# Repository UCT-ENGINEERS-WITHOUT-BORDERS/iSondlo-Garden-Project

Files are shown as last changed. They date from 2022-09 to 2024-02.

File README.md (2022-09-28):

# iSondlo-Garden-Project
For the management of work related to the Arduino-based electronic garden equipped with solar pv modules to generate power and sensors and internet connection capabilities to enable IoT features. Arduino-based embedded system includes temperature, humidity, and capacitive moisture sensors.

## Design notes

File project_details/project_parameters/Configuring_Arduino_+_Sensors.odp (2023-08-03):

## EWB iSondlo Project Configuring the Arduino & Sensors

20 October 2022

Electronics Team

## Scenario

- Garden in a 132cm x 379cm corrugated iron container
- Requires control and monitoring system to ensure that the environment yields high quality vegetables

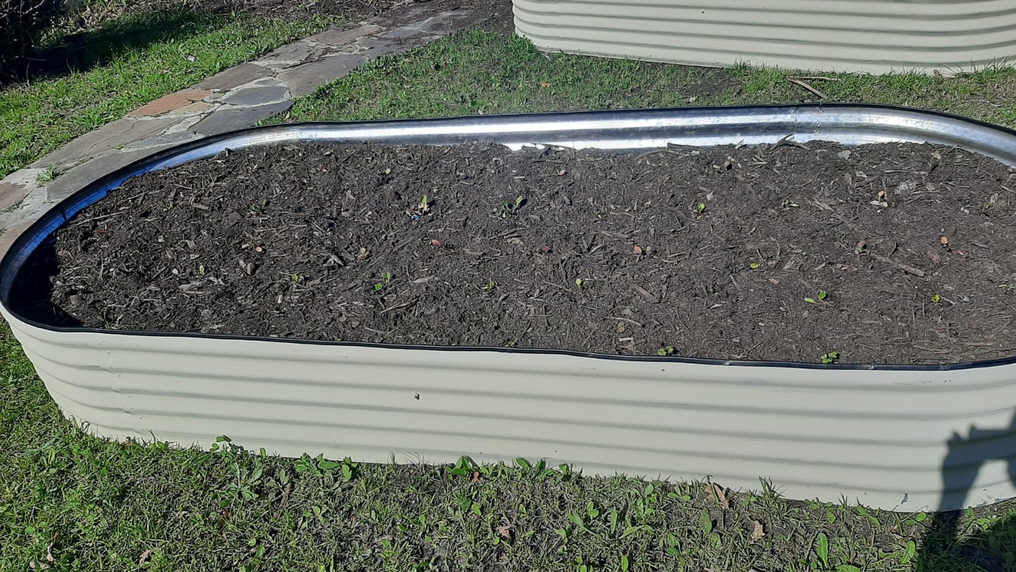
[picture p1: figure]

## Control and Monitoring System

- Garden is monitored using 4 sensors:
      - Temperature sensor:
          Maxim DS18B20 by Dallas Semiconductors
      - Soil moisture sensors:
          KE2023 Keyes moisture sensor module
      - Humidity sensor
          Ghitron HMZ-333A1
      - Light sensor
          LDR

## Control and Monitoring System

- Controls flow of water to plants using:
      - Relay switch
          KY0019 Keyestudio 5V Relay Module
      - Solenoid valve

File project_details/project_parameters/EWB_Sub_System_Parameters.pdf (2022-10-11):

Engineers Without Borders

Electronics Team:
iSondlo Garden Sub-System External Parameters and Constraints

Name: Bonga Njamela

### 10 October 2022

This aims to document the external parameters and constraints affecting the growth of plants in the iSondlo Garden. The main vegetable in the garden spinach (Spinacia oleracea).

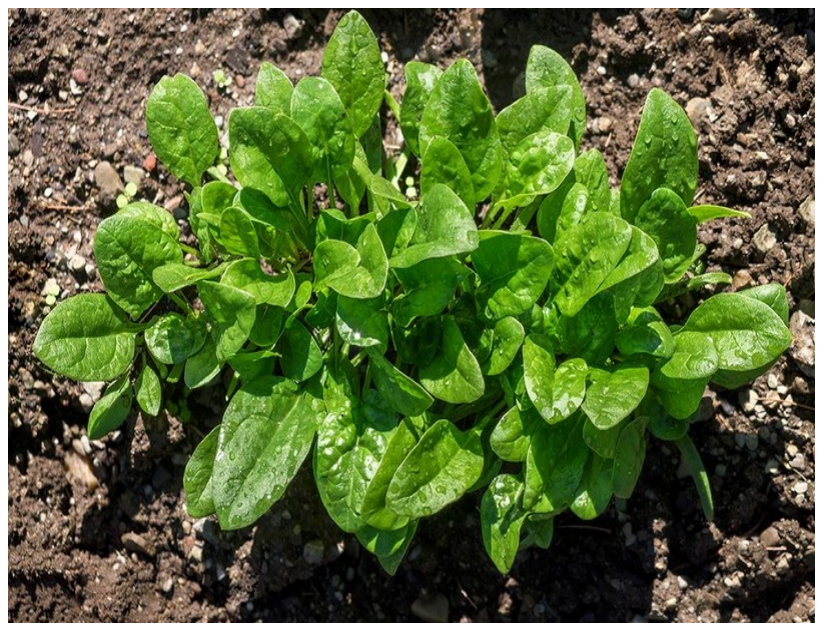
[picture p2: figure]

Some healthy looking spinach[1] (https://hips.hearstapps.com/hmg-prod/images/981/articles/2018/02/growingspinach-1000-0-1519138802.jpg)

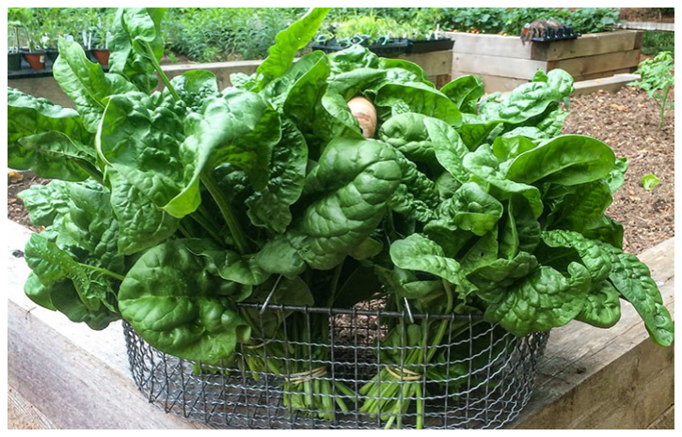
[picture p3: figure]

Ready to eat full grown spinach[2] (https://joegardener.com/wp-content/uploads/2021/04/IMG_1931-adj-708X466.jpg)

The state of the environment that the spinach grows in must be controlled to produce the best possible quality vegetable. The electronics team aims to maintain the optimum conditions for growth using an Arduino-based system. The system uses four sensors to monitor the state of the environment, namely, temperature; humidity; soil moisture; and light sensors. To maintain suitable conditions, the system controls the flow and distribution of water to the plants. We also aim to monitor and control the environment such that water is consumed in a sustainable manner.

This paper does not include the variables associated with the operation of the network connection module, and the storage and manipulation of data in the SD card module. Plant description

Spinach is a leafy vegetable which grows well in cool weather and in full sun to light shade. There are different types of spinach but each typically has smooth green leaves on a stem that grows vertically up from the soil. Spinach produces yellowish green flowers before seeding. It grows to maturity in six to eight weeks with leaves reaching 10 cm to

17 cm at maturity. It is recommended to plant spinach seeds in cool soil temperatures between 7℃ to 15℃ and to maintain the soil temperature between 16℃ and 24℃ after germination. Temperatures above the recommended range affect the taste of the spinach, making it taste more bitter. The soil moisture can be maintained and the temperature kept cool by adding mulch to the soil. The highest recorded temperature in Cape Town, in 2022, was recorded in February at 32.28℃ and the lowest recorded temperature was 8.33℃ in June[3] (https://www.ncei.noaa.gov/access/past-weather/cape%20town)

. The average temperature in between October 2021 and October 2022 was 16.11℃.

Graph showing maximum temperature trends around Cape Town International Airport[4] (https://www.ncei.noaa.gov/access/past-weather/cape%20town)

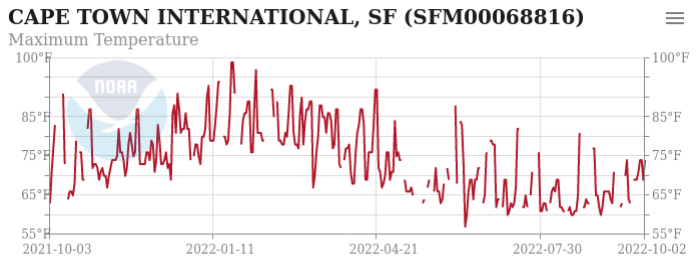
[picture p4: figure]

Spinach grows taller for days longer than 14 hours but if incident light is too bright and the temperature is too high, the plant will grow its floral stem prematurely. It requires constant soil moisture and humidity. The recommended humidity for the plants should be in the range of 90%-95%. In Cape Town, the relative humidity of the air ranges between 70% in November to 85%. Howevev, if the soil moisture and temperature needs are met, then humidity is typically not an issue.

Spinach requires to be watered frequently but without making the soil to soggy as the it will struggle to grow. Watering frequently becomes very important on days with high temperature to prohibit premature flowering. It is recommend to give spinach 2.54 cm to 3.81 cm of water per week[5]. (https://www.thespruce.com/growing-spinach-1403448) Values in this range should be achieved as an average of watering periodically rather than deeply to avoid making the soil soggy.

Each sensor has an associated variable to monitor and the Arduino is given low-value triggers, high-triggers and baselines corresponding to the recommended threshold values for each variable. To obtain suitable measurements of soil moisture, the soil moisture sensor should be calibrated to give values between 300 and 700 for 2.54 cm to 3.81 cm of water. The automated irrigation system should be calibrated to dispense the correct amount of water each time by measure the amount of time that the solenoid valve should be open.

Constant Variables and Monitored Variables

Table 1 on summarises the variables that are going to be monitored and the low-value triggers and high-value triggers associated with the minimum and maximum values for growing good quality spinach.

Table 1: Showing the variables that will be programmed in the Arduino to ensure optimum plant growth

Sensor Model and function | Variables | Description | Initial Value
| uint8_t MIN_TEMP | Constant minimum recorded temperature based on historical climate data [in ℃] | 8
| uint8_t MAX_TEMP | Constant maximum recorded temperature based on historical climate data [in ℃] | 32
| uint8_t MIN_SEED_TEMP | Constant minimum tolerable temperature before germination [in ℃] | 7
| uint8_t MAX_SEED_TEMP | Constant maximum tolerable temperature before germination [in ℃] | 14
| uint8_t MIN_SPIN_TEMP | Constant minimum tolerable temperature after germination [in ℃] | 16
| uint8_t MAX_SPIN_TEMP | Constant maximum tolerable temperature after germination [in ℃] | 24
| uint16_t hourlyTemp1 | Determined from the digital 9 bit output value Stored hourly and reset | 0

MAXIM
DS18B20

Temperature
Sensor

| hourly.
uint8_t dailyMeanTemp | Variable calculated from the hourly temperature. Store and reset daily. | 0
uint8_t weeklyMeanTemp | Variable calculated from daily average. Stored and reset weekly. | 0
uint8_t monthlyMeanTemp | Variable calculated from weekly average. | 0
uint8_t MIN_Humidity | Minimum relative humidity of the air that can be expected in Cape Town during the year [%] | 40
uint8_t MAX_Humidity | Maximum relative humidity of the air that can be expected in Cape Town during the year [%] | 85
uint8_t hourlyHumidity3 | Relative humidity determined from the DC output of the sensor every 3 hours and is stored and cleared hourly. | 0
uint8_t dailyMeanHumidity | Computed from the hourlyHumidity. Stored and cleared after computing weekly average relative humidity. | 0

Ghitron
HMZ-333A1

Humidity
Sensor

KEYES
KE2023

Soil Moisture
Sensor
uint8_t MIN_MOISTURE | Minimum value associated with humid soil. Sensor has values in the range [300, 700] for humid soil. | 310
uint8_t MAX_MOISTURE | Minimum value associated with humid soil. Sensor has values in the range [300, 700] for humid soil. | 650
uint8_t hourlyMoisture1 | Soil moisture recorded hourly. If this value is smaller than MIN_MOISTURE, the valve in the irrigation system is opened. Otherwise the valve remains closed. | 0
uint8_t dailyMeanMoisture | Average soil moisture computed daily. Used to keep track of daily water consumption for sustainable water usage. | 0
uint8_t weeklyMeanMoisture | Average soil moisture computed weekly. Used to ensure that water is used sustainably. Result is compared to growth of plants over a week. | 0
uint8_t monthlyMeanMoistur e | Average soil moisture computed monthly. Used to ensure that water is used sustainably. Result is compared to the condition of the plant over a month. | 0

LDRs

Light Sensor

uint8_t MIN_LIGHT | Corresponds to the value obtained from the LDRs when the LDRs are completely shaded [%] | 0
uint8_t MAX_LIGHT | Corresponds to the value obtained from the LDRs when the LDRs are completely illuminated [%]. | 100
uint8_t currentLight | The current value obtain from the LDRs. | 0
boolean lightOK | True if the value of the currentLight is greater than or equal to 50% otherwise the value is stored and a warning is transmitted. | false

The soil moisture sensor, humidity sensor and LDRs need to be calibrated to produced the desired values for computation. For example, more than one LDR can be used in a Wheatstone bridge configuration to achieve a linear relationship between the amount of incident light and the amplitude of the voltage signal received by the Arduino. The value of the output from the LDRs when they are completely occluded will correspond to a value of 0%. The values of the output that are higher than the value obtained when the LDRs are in sunlight on a sunny day correspond to 100%.

Variables related to the control of the system are included in the table below. These include the time-keeping capabilities which allow for recording values and operating the solenoid valve in the irrigation system. Some of the values have yet to be calibrated to ensure that resources are distributed in an effective and sustainable way.

Control Variables

Table 2: Showing the control variables used to maintain the good conditions for plant growth

Variable Name | Type | Description
startDate | struct | Value of the date recorded when the seeds are planted in the form DD:MM:YYYY where each variable is of type uint8_t.
endDate | struct | Value of the date recorded when the plants are harvested in the form DD:MM:YYYY where each variable is of type uint8_t.
currentDate | struct | Value of today’s date in the form DD:MM:YYYY where each variable is of type uint8_t.
currentTime | uint8_t | Network time for measuring when a unit of time (hours, days, weeks and months) have elapsed.
HOUR | uint8_t | Network time (currentTime) plus 60 minutes.
DAY | uint8_t | Network time (currentTime) plus 24 hours.
WEEK | uint8_t | DAY*7.
MONTH | uint8_t | Network time (currentTime) plus 27, 28, 29 or 30 days.
valveStatus | int | Value showing the status of the solenoid valve. If the value is -1, then the relay switch to the solenoid valve is not connected. If it is 0, then the valve is connected but is not operational. If the status is 1, then the valve is

| | operational.
valveOnTime | uint8_t | Computed from the value of the soil moisture and humidity to determine the length of time that the valve should be opened for. The larger the value of the soil moisture, the shorter the amount of time the valve should be opened. High relative humidity values (above 75%) reduce the value.

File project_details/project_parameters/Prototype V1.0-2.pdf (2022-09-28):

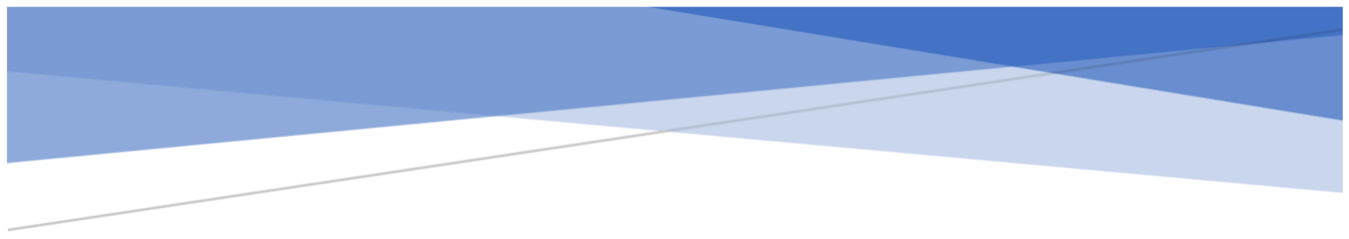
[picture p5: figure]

# ISONDLO ELECTRONICS TEAM Prototype System V1.0

## Engineers Without Borders - UCT

Team Leader: Benjamin Connolly

cnnben002@myuct.ac.za

iSondlo Electronics Team – EWB – UCT | 8/20/21

## Table of Contents

## Introduction

This document serves to record the progress and design process of the electronic engineering team working on the iSondlo garden project as we move into the prototype phase of the project.

The decision was made to split the electronics team into two sub-teams. This was so that two teams could work simultaneously on their parts independently of one another. This will hopefully increase overall team efficiency.

The power and solar team are responsible for the generation, manipulation, and storage of electricity generated through solar energy. They will also be responsible for the distribution of electricity for the entire electronics system and making sure that individual component’s specific power requirements are met.

The control and monitoring team is responsible for the collection of data via sensors, controlling the electrical system and outputs using microprocessors, and creating an app that allows a user to view data and turn on a valve (to control the watering system).

## Team Members

Control and Monitoring

- Ben Connolly (Lead)
- Heather Wimberley
- Justine Marie Pauline Bouchard
- Umutesa Munyurangabo
- Zuleigha Patel
- Bonga Njamela

Power and Solar

- Given Kibanza (Lead)
- Nozipho Sibanda
- Fhatani Netshirembe
- Antony Mason-Gordon
- Sampson Nwachukwu
- Bonga Njamela

## Control and Monitoring Team

Requirements
Monitoring Requirements
- Soil moisture
- Humidity
- Temperature
- Sunlight levels
- Sensors will need to be weatherproofed

Control System Requirements

- Log sensor data
- Interface with app
- Control water valve
- Will need to have cellular connectivity (optional for this prototype)
- Components will need to be protected from the elements

App Requirements

- Display weather patterns for site
- Sensor data displays
- Control irrigation system via valve
- Notification system

Solenoid Valve Requirements

- Must be a 12V valve
- Valve must open and close (try choose normally closed valve)

Block Diagram

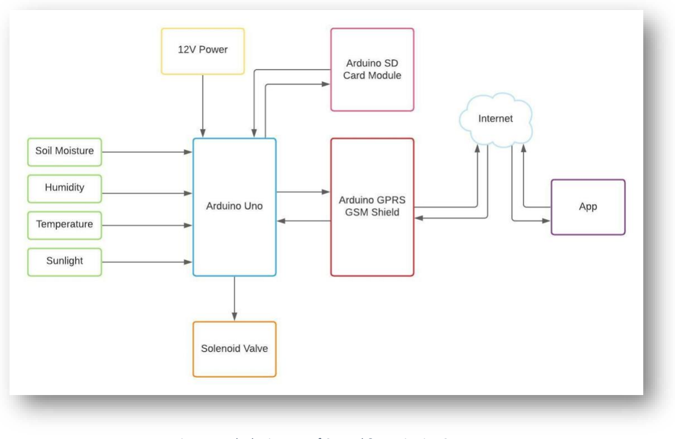
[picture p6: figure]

Figure 1 - Block Diagram of Control & Monitoring System

Microcontroller Design

Originally in the ideation phase, we had planned on using a combination of a Raspberry Pi and an Arduino Uno. This design was chosen so that we could expand the system if needs be by having the Raspberry Pi as the main computing chip and then Arduinos could be added onto that to extend the number of inputs/outputs that the system could handle. This was also when the site was close to Wi-fi which the Raspberry Pi could connect to so that we could send/receive data via an app. Circumstances have changed, we are now at a different site which is not close to Wi-fi which called for a new design.

From the block diagram, we can see that the new design features only an Arduino Uno as the only microcontroller. The Arduino will have a GPRS GSM Shield which attaches to it and this will give the Arduino full cellular capabilities – this helps us navigate the problem of no Wi-Fi on site.

Advantages of using this newer design:

- Simpler system as everything is Arduino Based
- A uniform programming language can be used
- Cheaper as we aren’t utilising the expensive raspberry pi
- Easy to expand
- Power can come directly from 12V batteries and doesn’t need to be regulated

An image of the GPRS GSM Shield that could be used is below:

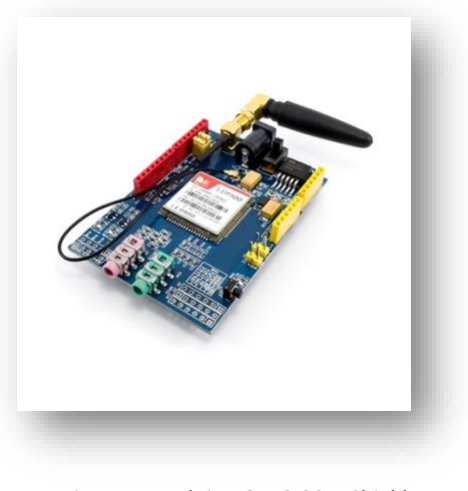
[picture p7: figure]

Figure 2 - Arduino GPRS GSM Shield

Here is a link to a helpful tutorial explaining how to set up and use the GPRS GSM Shield -https://www.arduino.cc/en/Guide/ArduinoGSMShield

From the block diagram in Figure 2, we can see that the new design features an Arduino SD Card Module which attaches to it and this will give the Arduino full data logging capabilities – this helps us navigate the problem of having no off-site server.

Advantages of using this newer SD Card Module design:

- Simpler system as everything is Arduino Based
- A uniform programming language can be used
- Cheaper as we aren’t utilising the expensive raspberry pi
- Easy to expand by purchasing an SD card that stores more data

An image of the SD Card Module that could be used is below:

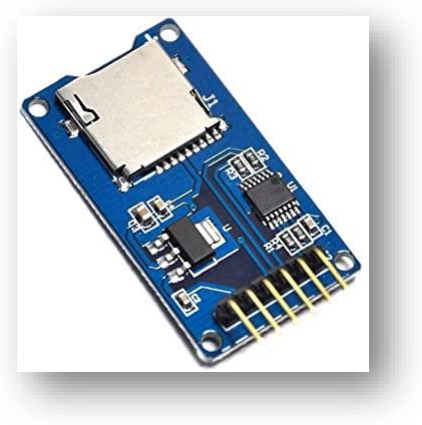
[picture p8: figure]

Figure 3 - SD Card Module

Required Components:

- Arduino Uno
- Arduino GSM GPRS Shield
- Sim Card + Data (500 MB)
- Arduino Micro SD Card Module
- Micro SD Card
- Capacitive Soil Moisture Sensor
- Humidity Sensor
- Waterproof Temperature Sensor
- LDRs

Expansion

Important: This prototype will not be testing the expansion capabilities of the design, this is just for future reference

Expansion is important as we move forward into the fully scaled design and is relatively easy with this design. When we think of expanding our system, we think of adding a lot more sensors to our garden, the Arduino only has a limited number of ports so expansion requires us to extend the number of ports of the Arduino. The easiest way to do this is to daisy chain multiple Arduinos together via the serial port and we can then set up code so that they communicate in that way. The picture of the basic set-up will be as follows:

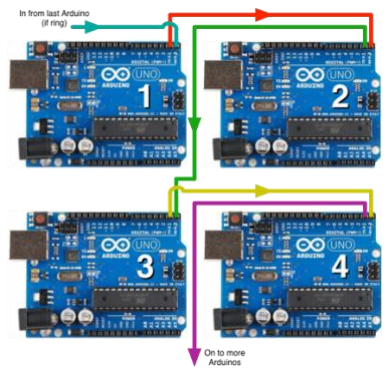
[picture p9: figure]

Figure 4 - Daisy Chained Arduinos

A helpful blog outlining the daisy-chaining process can be found here -http://www.wintergroundfairlands.com/2012/12/daisy-chaining-serial-connections.html

App

For the app, a node-red server was first thought of in the ideation phase. This is a good idea, but incredibly complex and time-consuming to set up, would require capital to pay for a dedicated server, and would be hard to make the display incredibly user-friendly. The solution is Blynk.

Figure 5 - Blynk Logo

Blynk is an app dedicated to prototype, deploy, and remotely manage connected electronic devices at any scale. This has a range of bonuses which include:

- Drastically more simple and easier to use
- Lots of existing documentation and support
- Offers budget-friendly and free options
- Blynk hosts the app on their servers
- Quick deployment and testing
- No need to spend hours programming an app

The Blynk app would allow us to completely customise our homepage to suit our needs. For example, we can add graphs only the sensors we need and display current data readings. An example of what our homepage could look like is below.

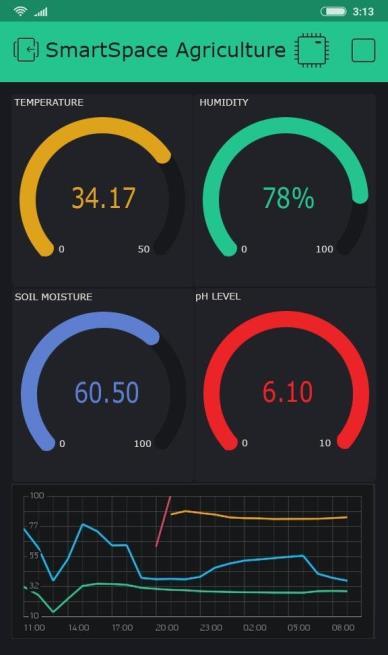
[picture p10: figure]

Figure 6 - Possible Blynk Home Screen

The figure below gives a good overview of how the overall system connects together.

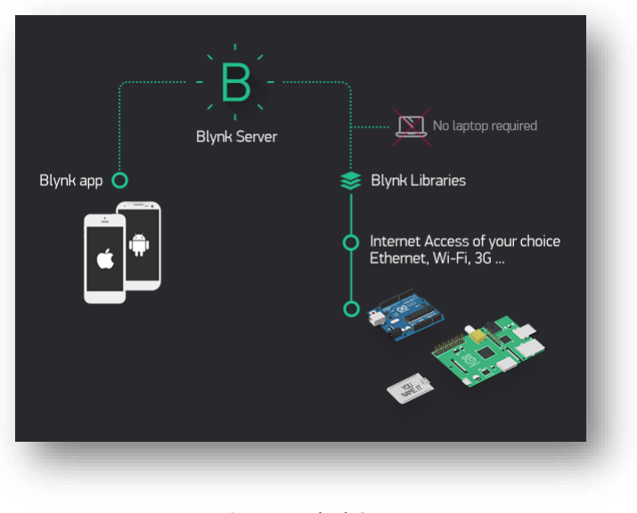
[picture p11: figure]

Figure 7 - Blynk System

Another great bonus of using Blynk is that it integrates perfectly with our current design. The Arduino’s GPRS GSM Shield will connect directly to our Blynk app via the internet and will allow us to get real-time information about our system.

This would be a great choice because it meets the following iSondlo requirements for the app:

- It will allow us to remotely control the irrigation system using a solenoid valve
- It will display current data readings such as soil moisture/humidity/temperature etc.
- It will log previous data readings
- It has an inbuilt notification system so that users can get notifications if certain garden parameters are below a certain threshold

Required Components:

- Blynk App

Solenoid Valve System

A figure of the solenoid valve system:

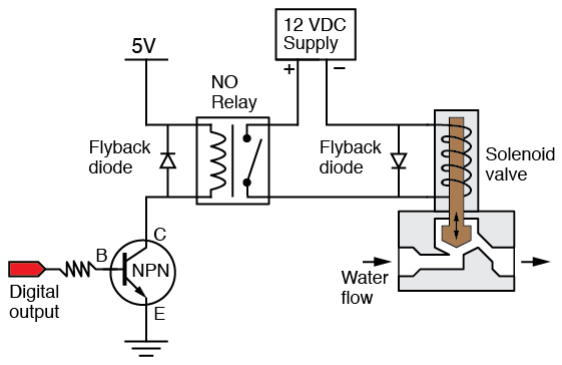
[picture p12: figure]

Figure 8 – Solenoid Valve System Overview

Image source:
https://web.cecs.pdx.edu/~eas199/B/howto/fishtank/wiring/img/transistor_relay_solenoid_valve_flyback.png (https://web.cecs.pdx.edu/~eas199/B/howto/fishtank/wiring/img/transistor_relay_solenoid_valve_flyback.png)

The logic behind the system is quite simple. The Arduino will have a dedicated digital output pin which will in turn control an NPN resistor. This resistor in turn will control a relay circuit that controls the solenoid valve. The Arduino will connect to the internet and interface via the Blynk App so that the solenoid valve can be controlled remotely.

The smaller components such as the resistors and diodes will be calculated once we know what relay and solenoid valve is going to be used exactly. This will not hinder our progress as these components are readily available from UCT’s White and SASOL Electronics Lab.

Required Components:

- Relay Switch (min rating 10V, 2A, 20W)
- Solenoid Valve (DC 12V, 1A max)
- Resistors
- 2N222A NPN Transistor
- 1N4001 Diode

Weatherproofing

Soil Moisture Sensors

After doing online research, we are going to waterproof the connections and electronics of our capacitive soil moisture sensors following this tutorial: https://www.instructables.com/Waterproofing-a-Capacitance-Soil-Moisture-Sensor/

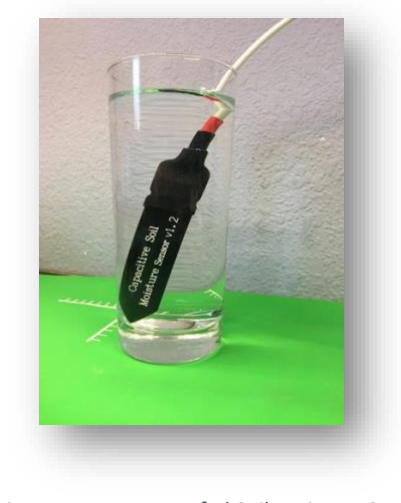
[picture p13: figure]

Figure 9 - Waterproofed Soil Moisture Sensor

Required Components:

- Adhesive lined polyolefin Heat-shrink tubing ¼ inch
- Adhesive lined polyolefin Heat-shrink tubing ½ inch
- Adhesive lined polyolefin Heat-shrink tubing ¾ inch
- Nail Polish
- Heat Gun/Hairdryer

Temperature Sensor

The temperature sensor chosen are waterproof ones so no waterproofing was needed.

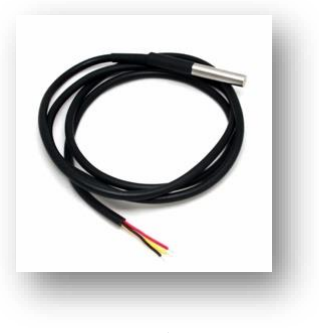
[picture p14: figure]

Figure 10 - Waterproof Temperature Sensor

Light Dependent Resistors

It was quite tricky coming up with a system to waterproof the LDR because the entire component needed to be waterproofed including its connection points. Ultimately we decided to go with clear-set epoxy glue. This would allow us to cover the entire component and all its connections in one go as well as allowing it to still detect light. We could also add a stake/skewer into the epoxy before it sets so that the LDR can easily be stuck into the ground.

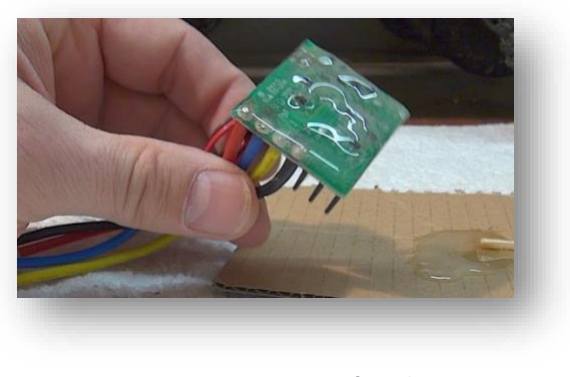
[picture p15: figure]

Figure 11 - Epoxy Waterproofing Electronics

Required Components:

- Clear Set Epoxy Glue
- Garden Stake/Skewer

Control Housing

The control hosing will simply be a clear plastic Tupperware. This will protect it from the elements and will provide easy access when needed. The seal provides a fully watertight seal around the container lid. The various wires coming in and out of the control housing will be through drilled holes and sealed off with clear set epoxy glue.

Required Components:

- Tupperware (420ml)
- Clear Set Epoxy

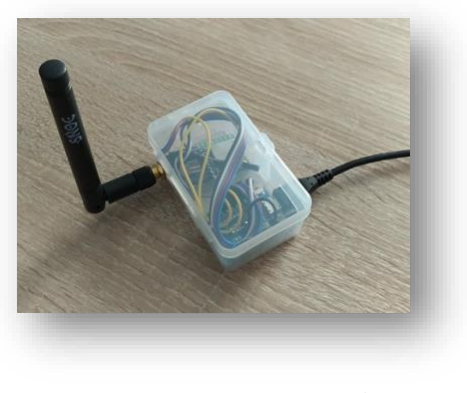
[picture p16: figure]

Figure 12 - Tupperware Protecting Electronics

Signal Wires & Other Connections

The signal wires (wires carrying signals and voltages between the various components) need to be waterproof rated if they are not enclosed in a watertight housing. This is extremely important because if waterproofed properly and water enters the system, there could be electrical fires and electrocution may occur damaging property, buildings and people. Similarly, all exposed connections need to be sealed off with epoxy glue.

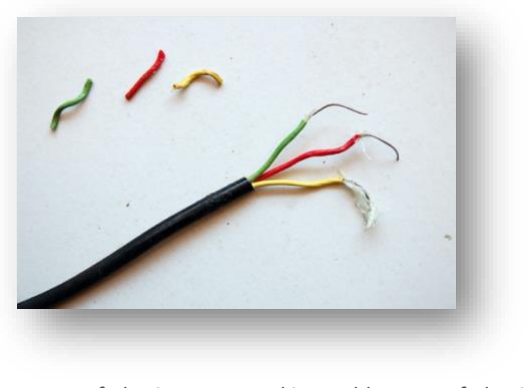
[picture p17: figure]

Figure 13 – Waterproofed Wires Wrapped in Double Layer of Plastic Protection

Required Components:

- Outdoor Rated & Waterproof Wires
- Clear Set Epoxy

For future reference, but not necessary for this prototype: When implementing this system into the garden it would be good to bury the cabling deep underground as not to be accidentally broken while gardening and make use of PVC piping to provide an extra layer of protection.

Testing

To test our system, we plan on setting up a miniature garden in one of the UCT labs. We will have a small pot which we can water to test our soil moisture sensor, we can simulate sun for our LDR’s using a light on our phone, we can measure our temperature and humidity reading vs what the weather app is saying for our area.

The control system and app will either work or won’t work so it will be easy to tell if we are on the right track or not.

The solenoid valve system will require us to connect two pipes with the solenoid valve in the middle. We can then fill the top half with water and when we active the solenoid valve, water should hopefully flow down into the second pipe and into a bucket.

We would also like to heavily test the weather-proofness of our system by extensively testing our waterproofed components and making sure that not even a drop of water manages to penetrate through to the electronics.

Required Components:

- Bucket
- ½ inch tubing

Schematics

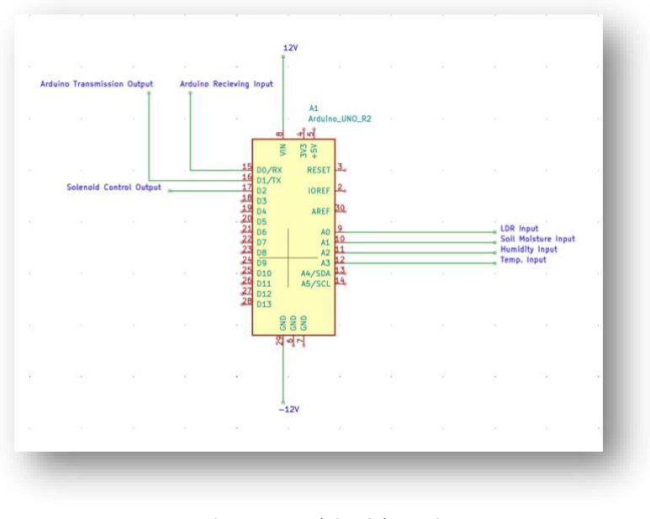
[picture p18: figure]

Figure 14 - Arduino Schematic

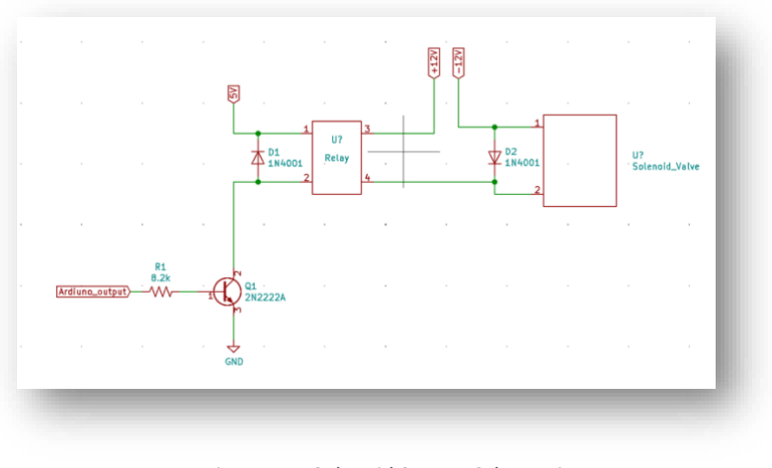
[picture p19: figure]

Figure 15 - Solenoid System Schematic

What We Are Aiming To Do Next

- Get iSondlo’s Feedback
- Source our components
- Build our system
- Test our system
- Make a list of our shortcomings and find ways to fix them
- Start thinking about implementing this into the next prototype version or the iSondlo garden

## Power & Solar Team

Requirements
Solar Requirements
- Perform power calculations to determine the power consumption of the electronics system.
- Design a solar system that will cater to these needs. Additionally select the components needed for the system; solar panel, charge controller, batteries, etc.

For this prototype, the solar system needs to be able to power the entire electronics system and should store enough power to keep the system running for a few hours after the solar panel stops producing electricity (aka. It gets dark).

When coming up with the design take into account that this is just our prototype system and that the final version will have a much greater power storage need. Therefore, start small and try to make the design modular so that we can upgrade the solar system when the time comes. It is important to outline how the expansion process will take place.

- The batteries should output 12V.
- Solar system must be weatherproof.

Power Monitoring Requirements

Important: This will not be done in this prototype.

These requirements are time permitting and may only be implemented in a future prototype.

- Design a monitoring system that provides real-time information on the solar system nodes. This should be able to link up with the Arduino and the app so that the user can see what is happening with regards to the power generation/consumption/storage.

Block Diagram

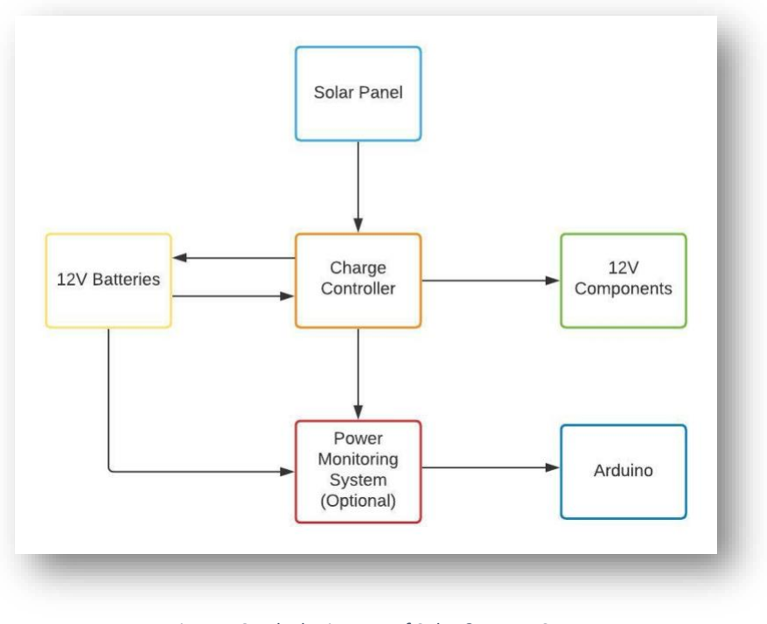
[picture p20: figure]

Figure 16 - Block Diagram of Solar & Power System

Power Calculations

Device | Max Voltage (V) | Max Current (A) | Power (W)
Arduino Uno | 6 | 2 | 12
Solenoid Valve | 12 | 1 | 12
Total Power: | | | 24

Since all the sensors/modules interface with the Arduino, we only need to take the Arduino’s maximum power consumption into account. We also didn’t need to take into account any of the other teams’ power consumption needs for this prototype.

From the above table, we can see that the power that the system consumes is 24 Watts.

Solar Panel

From the above power calculations, we can see that we will need a solar panel that is capable of providing at least 24W to power the system. We will also need to double that power generation if we want to store enough power to last us during the night/rainy days. We have decided to go with one 50W solar panel in order to achieve this.

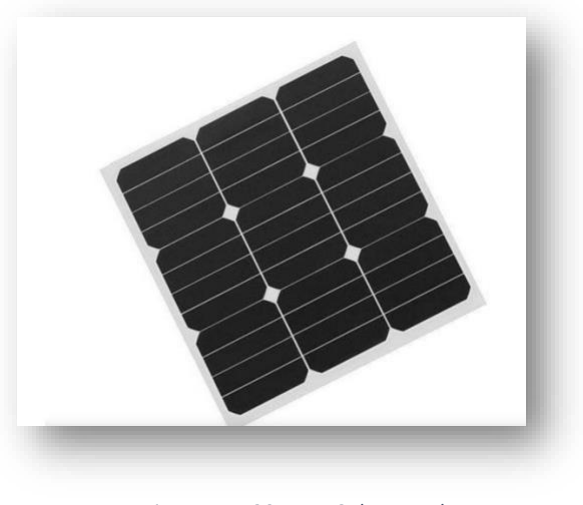
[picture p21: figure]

Figure 17 - 30 Watt Solar Panel

The solar panels will be connected to the charge controller.

Required Component:

- 50W Solar Panels (12V, 2.5A )

Charge Controller

The charge controller of the system is the ‘power management system’. The electronics inside regulate the voltages and currents coming in from the solar panel and then charges the battery in a stable way. It also takes the power from the batteries and provides a stable voltage to the control and solenoid system. It also prevents overcharging and electrical spikes.

We had to choose between using a Pulse Width Modulation (PWM) charge controller or a Maximum Power Point Tracking (MPPT) charge controller. Both have their advantages and disadvantages. After doing our research, we have decided to go with the PWM charge controller and its advantages are as follows:

- Simpler design
- Cheaper
- Better suited for small solar systems
- Reduces the power entering the battery as it approaches its maximum charge (prevents overcharging)

The following figure shows how the charge controller will integrate with the rest of the design:

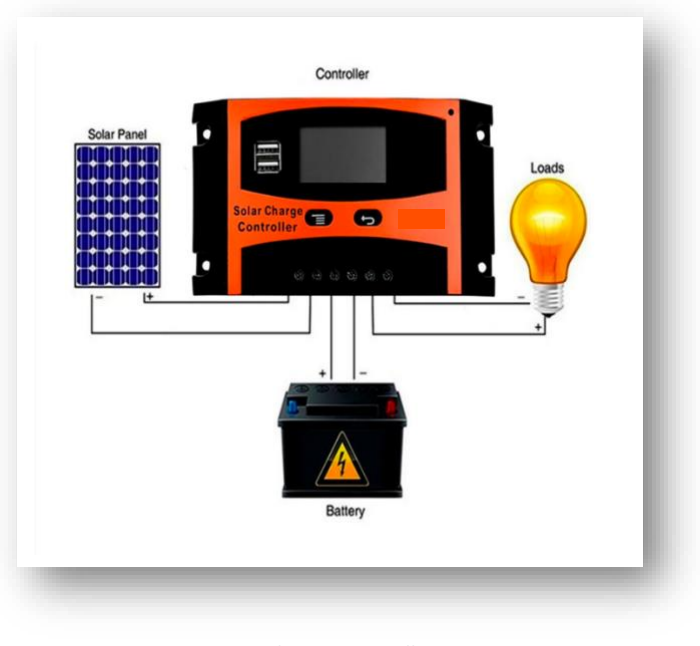
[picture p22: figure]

Figure 18 - Charge Controller Integration

Required Components:

- Charge Controller (12V, 5A min)

Batteries

When choosing a battery to store our power, we had two battery types to choose from (lead-acid or lithium-ion) and 3 main categories to focus on:

- Cost
- Energy density
- Charging

Taking the above into account, it seems unnecessary to be searching for a lithium ion option for early stage prototyping. The energy demands of the iSondlo electronics are significantly lower than that required in industrial applications where lithium-ion would be better suited. Additionally, the cost benefit of lead acid batteries are a significant factor at this stage of design.

Important: It must be noted however that not all batteries are self-contained/protected from weather conditions and should be housed appropriately (but not sealed).

For our prototype system, we will be making use of a 12V, 2.4Ah lead-acid battery. This should power our system for over an hour once the solar panel cuts out (from not enough sunlight).

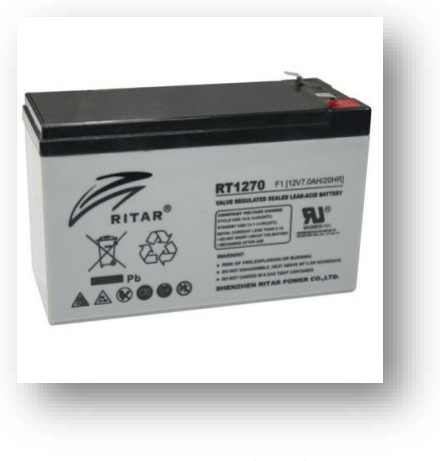
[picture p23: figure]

Figure 19 - 12V Lead-Acid Battery

Required Components:

- Lead Acid Battery (12V, 2.4 Ah)

Testing

After the system's configuration, it will thoroughly be tested to ensure proper performance and safe operation. The following tests will be carried out during and after the installation of the system:

- Continuity and resistance testing: This process will be performed to ensure that the conductors and other terminations are well grounded.
- Polarity testing: At this stage, the polarity of the battery, charge controller, and solar panel will be verified.
- Voltage and current testing: This will be performed to ensure that the solar panel, battery, and the power inverter's operating parameters are within the required/expected specifications.
- Performance testing: This will also be performed to ensure that the system power and energy outputs correspond with the expected values.
- System functional testing: This test will be used to determine that the system is working correctly and within the required or nominal limit. It involves starting up, shutting down, and checking the nominal operating conditions of the system.

Expansion

Since the this stage of the project is a prototype, there will be scaling up the capacity of the system in the future. Therefore, the following components/parts will be scaled up when the time comes:

- Battery
- Charge Controller
- Solar Panel
- Batteries

The capacity of the battery needed in this project depends on the total load requirement of the entire system. The higher the load capacity, the higher the battery's capacity, which also depends on the number of hours the system will be ON. Since the project is at the prototype stage, it may require a low-capacity battery, but it can continually be expanded by performing a simple system load analysis/calculation and adding more batteries connected in parallel as needed.

The capacity of the charge controller will be expanded as long as there is a significant increase in the number and capacity of the panels. Suppose the number and capacity of the panels that will be installed in the future are more than the capacity of the charge controller installed initially. In that case, the capacity of the new controller will be determined by calculating the total output current and voltage of the solar panel(s). With our current charge controller, we can double the size of the system without needing to upgrade it.

What We Are Aiming To Do Next

- Get iSondlo’s Feedback
- Source our components
- Build our system
- Test our system
- Make a list of our shortcomings and find ways to fix them
- Start thinking about implementing this into the next prototype version or the iSondlo garden
- Design and prototype weatherproofing for the system
- Design and prototype a monitoring system
- Design and prototype a mount for the solar panels

Just a note about the future prototyping of the solar mount system: This is currently being researched by the team and, considering all the factors involved, we did not feel comfortable including it in this prototype, but the following figure will provide a feel for the direction we are going in.

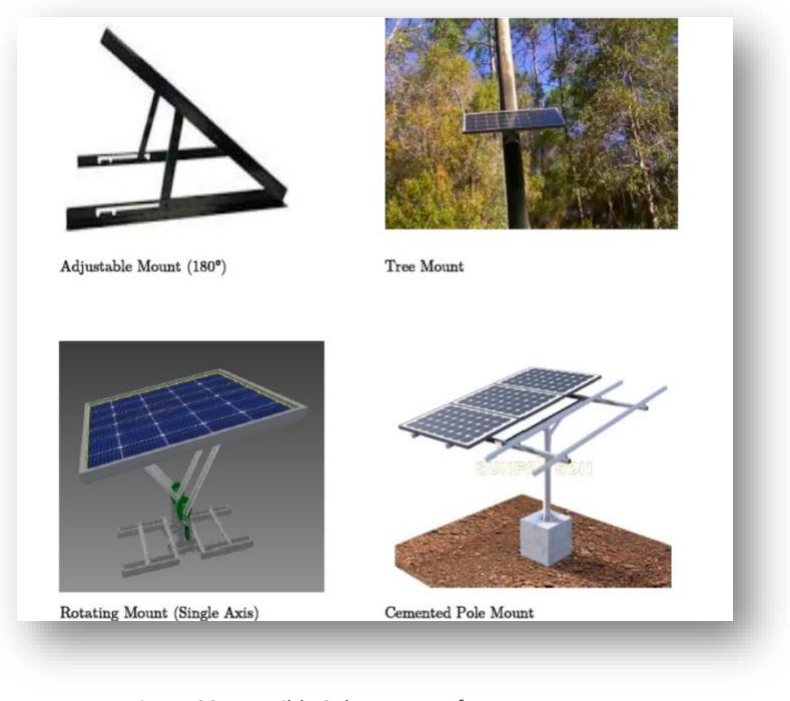
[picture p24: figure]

Figure 20 - Possible Solar Mounts for Future Prototypes

## Bill of Materials and Estimated Expenses


Figure 21 - BOM & Estimated Costs


Figure 22 - Summary of Estimated Expenses

The estimated costs of our entire electronics prototype design came to a total of R3739.00. Unsurprisingly a big percentage of that cost came from the control and monitoring electronics and the solar equipment, but perhaps more surprising to the team was how much the weatherproofing is estimated to cost us.

We tried to source parts from the UCT electronics’ white lab where we could. However, you will notice that most of the components come from www.banggood.com and www.takealot.com . I’m sure that I don’t need to give Takealot any introduction, but banggood is a Chinese-based online retailer. I (the team leader) have used them many times, they have thousands of reputable reviews and most importantly they are much cheaper than local stores. I would suggest that we use the stores that are listed in the BOM to get our components. I have not taken into account the discounts, shipping costs, and insurance and therefore I would have a uncertainty percentage of 10%, bringing the total cost to R4113.00 . We would rather the team overshoots on the estimated costs and then give leftover money back to EWB than being held up by waiting for more cash to be released to us.

We would also like to point out that the prototype version for the control and monitoring team does not need a lot more capital to scale up to our full size. This initial prototype will most likely be our biggest expense and all the electronic equipment that passes our tests (which we expect all our equipment to do) in this prototype will go on into the final implementation.

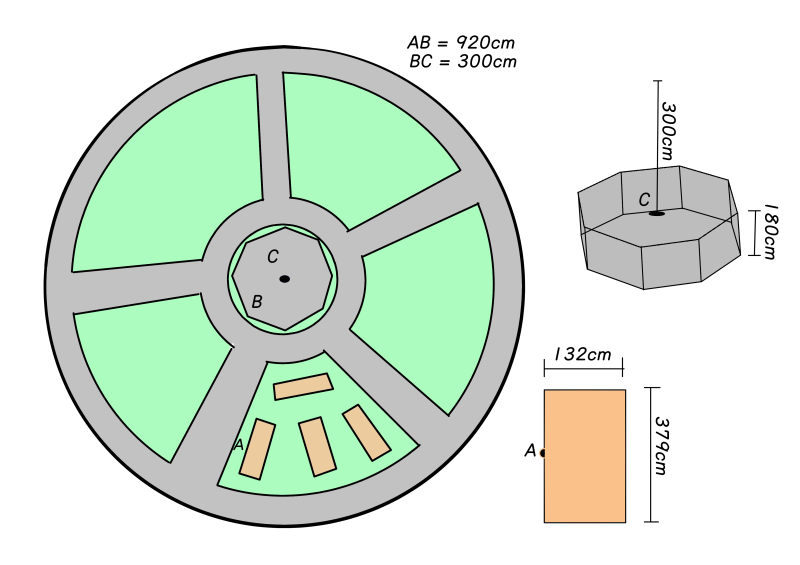
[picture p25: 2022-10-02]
project_details/project_parameters/EWB_Site_Dimensions.png

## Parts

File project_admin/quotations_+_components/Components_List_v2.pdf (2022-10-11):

University of Cape Town
Engineers Without Borders Society Electronics Team
Components List for Prototype v01

### 21 September 2022

This document shows updated lists of the components that are required to build a prototype for the iSondlo Garden Project. The electronics team was divided into the Power and Solar sub-team and the Control and Monitoring sub-team. As such, two tables are included, one for each team. These tables also show the vendors from which the components will be purchased and the price of each component on the date that the document was compiled. Components that can be obtained from the university show a dash for the cost. The total cost includes the shipping cost for components that need to be purchased online.

Table I: Components required by the Control and Monitoring Team for the construction of the prototype

Component | Specifications | Quantity | Vendor | Cost [in Rands]
Arduino Uno | Arduino UNO R3 develop. module board & lead | 1 | Mantech (https://www.mantech.co.za/ProductInfo.aspx?Item=13M2047-A) | 736.33
Arduino GSM GPRS Shield | SIM900 Quad Band GSM GPRS Shield, Embedded TCP/UDP | 1 | Mantech (https://www.mantech.co.za/ProductInfo.aspx?Item=15M8378) | 773.30
Bucket | 5l bucket | 1 | - | 20.00
Clear Set Epoxy Glue | Alcolin Epoxy Liquid Rapid Set Clear 2 x 20 ml | 2 | Makro (https://www.makro.co.za/hardware-auto/paint-surface/painting-accessories/adhesives/alcolin-2-x-20-ml-epoxy-liquid-rapid-set-clear-/p/000000000000400156_EA) | 98.00
Diode | Diode rectifier axial 50v 1a | 2 | Mantech (https://www.mantech.co.za/ProductInfo.aspx?Item=64M0063) | 0.57
Garden Stake/Skewer | Standard irrigation stake 200 mm | 1 | - | 20.00
Heat Gun/Hairdrye r | Black & Decker Heat Gun (1750W) | 1 | Makro (https://www.makro.co.za/hardware-auto/diy-powertools/diy-heat-guns/heat-guns/ryobi-2000-w-heat-gun-/p/000000000000197691_EA) | 599.00
Heat-shrink | ¼-inch, ½-inch, | 1 | Makro (https://www.makro.co.za/hardware-auto/electrical/pvc-conduit-electrical-accessories/pvc-conduits/steinel-shrink-tubing-iii---4-0-12-0-mm---heat-shrink-20pcs--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) | 130.00

Tubing | ¾-inch adhesive lined Polyolefin
Humidity Sensor | Humidity sensor board / module [GHITRON] | 1 | Mantech (https://www.mantech.co.za/ProductInfo.aspx?Item=82M1087) | 116.97
LDRs | LDR 3x4 RL=10K RD=1M MEC | 1 | Mantech (https://www.mantech.co.za/ProductInfo.aspx?Item=82M0498-A) | 19.00
Micro SD Card Module | Arduino Micro SD Card Reader Compatible with Arduino [KEYESTUDIO] | 1 | Mantech (https://www.mantech.co.za/ProductInfo.aspx?Item=15M8259) | 35.16
Nail Polish | For exposed circuits | 1 | - | 20.00
Relay Switch (min rating 10V, 2A, 20W) | 5V One 1 Channel Relay Module Board Shield with optocoupler Support High and Low Level Trigger. | 1 | Mantech (https://www.mantech.co.za/Stock.aspx?Query=relay+switch+5vand) | 22.54
Resistors | | 1 | - | -
Sim Card + Data (500 MB) | Vodacom SIM Card, 500MB x 3 months | 1 | Vodacom | 133.00
Soil Moisture Sensor | Capacitive type moisture sensor | 2 | Mantech (https://www.mantech.co.za/ProductInfo.aspx?Item=15M3309) | 32.13
Solenoid Valve | 3/4inch 12VDC SOLENOID VALVE, MAINS PRESSURE OPERA [EIE] | 1 | Mantech (https://www.mantech.co.za/ProductInfo.aspx?Item=15M4842) | 149.81
Tubing | 2 m, ½-inch Libra marketing PT011 Tubing | 1 | Makro (https://www.makro.co.za/home-garden/lawn-garden/water-storage/water-storage/pvc-12mm-clear-tubing---5m-roll/p/c7dc7305-2781-4d3d-b46b-09502f3f2dc3) | 104.50
Transistor | 2N222A NPN | 1 | - | -

Waterproof Temperature Sensor | Temperature Sensor - DS18B20 - 1M | 1 | Mantech (https://www.mantech.co.za/ProductInfo.aspx?Item=14M0403) | 49.00
| | | Total | 3059.31

Table II: Components required by the Power and Solar sub-team for the construction of the prototype

Component | Specifications | Quantity | Vendor | Cost [in Rands]
PV Module | CNBM 6M-55 55W Mono Solar Panel, max Vmp=18.6V, max Imp=2.96 A. | 1 | Solar-man (https://www.solarmansa.co.za/) | 2000.00
Battery | Solar Gel 12V Battery 33AH Deep Cycle | 1 | Solar-man (https://www.solarmansa.co.za/) | 1289.00
Cables* | - | - | - | -
Charge Controller | 10A, 133x70x35mm | 1 | Solar-man (https://www.solarmansa.co.za/) | 289.00
Mounting System* | Ballast mount | - | - | -
| | | Total* | 3578

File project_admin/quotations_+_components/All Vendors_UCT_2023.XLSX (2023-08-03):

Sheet: Vendors ALL
Vendor | Name 1 | Name 2 | City | Telephone 1 | Telephone 2 | Fax Number | VAT Registration No. | Clerk at vendor | BLK FEMALE | Accounting clerk's fax | Clerk's internet address | Accting clerk's telephone no.
200002 | Air Products South Africa Pty Ltd |  | KUILSRIVER | 021 9413961/3 |  | 021 9413981 | 4020120673 |  | 000566 |  | accounts_receivable@airproducts.co.za
200005 | A & A Furnishers |  | CAPE TOWN | (021) 4246150 |  | (021) 4233475 | 4830102218 |  | 021598 |  | beulah@aafurnishers.co.za
200014 | Afrox Ltd |  | JOHANNESBURG | 086 0020202 |  | 086 0020201 | 4120110541 |  | 000388 | 086 0020201 | clarissa.dangor@afrox.linde.com | 086 0020202
200016 | Atomic Office Equipment |  | MAITLAND | 021 5102145 |  | 021 5102181 | 4830101848 |  | 001163 |  | atomicaccounts@argent.co.za
200020 | B & H Plumbing Supplies Pty Ltd |  | MAITLAND | (021) 5110008 |  | (021) 5112536 | 4740101326 |  | 031801
200023 | B & M Scientific CC |  | PAROW INDUSTRIA | 021 9338132 |  | 021 9338931 | 4870119437 | Ghadija Jacobs | 047430 | 021 9338931 | Fatima@bmscientific.co.za | 021 9338132
200024 | Afcom Cape Pty Ltd |  | EPPINDUST | (021) 543491 |  | (021) 544847 | 4260103132 |  | 000337
200025 | Roche Diagnostics Pty Ltd |  | MIDRAND | 011 5044777 |  | 021 4480849 | 4420106256 |  | 002445 | 011 8862962 | maphefo.mphekgwane@roche.com | 011 5044768
200027 | Bluu Car Rental Pty Ltd |  | KEMPTON PARK | 021 4185232 |  | 021 4253216 | 4610293054 |  | 047899 |  | judkinst@bcr.co.za
200030 | Commercial & Industrial Cleaning | Supplies Pty Ltd | CAPE TOWN | (021) 0861 39... |  | (021) 086 5056689 | 4510101324 |  | 004944
200039 | Akkersdyk Studio CC |  | WYNBERG | 021 7624339 |  | 021 7626063 | 4300103779 |  | 000604 |  | akkersdykstudio08@gmail.com
200049 | Introstat Pty Ltd |  | HOWARD PLACE | 021 5307900 |  | 021 5307901 | 4790102042 |  | 032212 |  | dawnm@introstat.co.za
200052 | Lasec SA Pty Ltd |  | CAPE TOWN | 021 5317504 |  | 021 5317562 | 4320190434 | Nicky Bezuidenh | 011126 |  | debtors@lasec.com
200053 | Labscheme Allchem Plastics |  | ELSIES RIVER | 021 5939736 | (021) 5939734 | 021 5939735 | 4100117227 |  | 048461 |  | carmen@labschemeallchem.co.za
200056 | Alplas Shutters & Louvres Pty Ltd |  | CHEMPET | (021) 5515233 |  | (021) 5514272 | 488010326 |  | 000760
200060 | Alsafe Pty Ltd |  | MAITLAND | 021 5346451 |  | 021 5346709 | 4270241591 |  | 048488
200061 | First Technology (Western Cape) Pty |  | CENTURY CITY | 021 5257000 |  | 021 5257096 | 4190260929 | Karen Skeates |  | 021 5257095 | KarenS@FirstTechnology.co.za | 021 5257000
200066 | Ana-Digi Systems CC |  | BELLVILLE | (021) 9149030 |  | (021) 9149050 | 4160103661 |  | 052477
200067 | Orms CC |  | VLAEBERG | 021 4653573 | (021) 4653574 | 021 4652928 | 4720143900 |  | 053635 |  | accounts@orms.co.za
200068 | Anatech Instruments Pty Ltd |  | BELLVILLE | 021 9462207 | (021) 9462208 | 021 9464276 | 4850108905 |  | 000825 |  | debtors@anatech.co.za | 011 4626776
200082 | SAP Public Services (Pty)Ltd |  | GALLO MANOR, JOHANNESBURG | 011 2356000 |  | 011 2356001 | 4150190645 |  | 057398 |  | n.beukes@sap.com
200084 | Steiner Hygiene Pty Ltd |  | HOWARD PLACE | 021 5323045 |  | 021 5323047 | 4530176587 |  | 028533 |  | MarjorieS@steiner.co.za
200085 | Telfa Engineering Pty Ltd |  | KENWYN | 021 7041620 |  | 021 7041629 | 4620262230 | Monica Mudhari | 050563 | 021 7041629 | admin@telfa.co.za | 021 7041620
200090 | United Scientific (Pty) Ltd |  | CHEMPET | 021 5925240 |  | 021 5925048 | 4120132479 |  | 048976 |  | accounts@united-scientific.co.za
200092 | Vulcan Catering Equipment Pty Ltd |  | CAPE TOWN | (021) 5105010 |  | (021) 5103780 | 4500138450 |  | 020192 |  | islef@vulcan.co.za
200095 | Bidvest Office Pty Ltd | T/A Bidvest Waltons | Cape Town | 084 683 7202 |  | 021 4422101 | 4010107623 | Regan Momberg | 020478 | 086 6101035 | adielah.solomon@waltons.co.za | 021 4422498
200099 | Baltic Timber Co Pty Ltd |  | CAPE TOWN | 021 4484600 |  | 021 4485600 | 4740101342 | Charmaine | 001546 | 021 4485600 | accounts@baltic.co.za | 021 4484600
200101 | Lithotech Sales Cape (Pty) Ltd |  | EPPINDUST | 021 5074100 |  |  | 4520101496 | Ashley Willemse | 001627 |  | ashleyw@lithotech.co.za | 021 5074100
200103 | Altron TMT Pty Ltd |  | CAPE TOWN | 021 5122710 |  | 021 5113858 | 4320267851 | S.Groenewald | 016330 |  | Shannon.Groenewald@altron.com
200109 | Caldis Sound & Furniture |  | CAPE TOWN | (021) 4234868 | (021) | (021) 4242789 | 4260112448 |  | 055689
200110 | Beckman Coulter South Africa Pty | Ltd | HALFWAY HOUSE | 021 5317402 |  | 021 5311743 | 4520102841 | Johan Dicks | 001902 | 086 6716945 | bcsaremittances@beckman.com | 011 5643265
200117 | Camquip Trading CC |  | FOURWAYS | 011 7040892 |  | 086 6113255 | 4730105055 | Brendan Pursey | 032646 | 086 6113255 | leefilters@camquipsa.co.za | 011 7040892
200122 | Cape Agricultural Products |  | SOMERSET WEST | 021 8525708 | (021) 8525709 | 021 8511369 | 4340137498 | Anita Robinsen | 054534 | 021 8511369 | anita@capeag.co.za | 021 8525708
200123 | Beshgro Pty Ltd t/a Bolt & Nut Cent |  | PAARDEN EILAND | 021 5112087 |  | 021 5117552 | 4550117818 |  | 002534
200130 | Britechem Pty Ltd |  | GREEN POINT | 021 9323208 |  | 021 9321259 | 4450101771 |  | 031100
200133 | Cape Cables Pty Ltd |  | RONDEBOSCH | 021 5110340 |  | 021 5117469 | 4610121461 |  | 048615 |  | tracey@smartoffice-ct.co.za
200138 | Cape Gate Fence & Wire Works | Pty Ltd | PAROW | 021 9311351 |  | 021 9318724 | 4100110834 |  | 003476 |  | Ingrid@capegate.co.za
200142 | New Africa Books (Pty) Ltd |  | GLOSDERRY | (021) 6744136 |  | (021) 6743358 | 4600103600 |  | 015156
200143 | The Artists Edge Pty Ltd | t/a The Deckle Edge | HOUT BAY | 021 4486800 |  | 021 4486940 | 4300300540 |  | 053759 |  | peter@deckleedge.co.za
200144 | Cape Instrument Services CC |  | PAARDEN EILAND | 021 5114104 |  | 021 5119866 | 4050103771 |  | 050407
200146 | Cape Key & Locksmith Suppliers | Pty Ltd | WOODSTOCK | 021 4477070 |  | 021 4475150 | 4930123403 |  | 003506
200148 | Independent Newspaper Pty Ltd |  | JOHANNESBURG | 086 0332927 |  | 011 8368553 | 4390149203 |  | 000019 |  | anathi.wezo@inl.co.za
200153 | Diagnostic Products CC |  | RANDBURG | 011 8861640 |  | 011 8867600 | 4510127154 | C. Maitland | 031550 | 011 8867600 | caronm@dpcrsa.co.za | 011 8861640
200154 | Cape Pottery Supplies CC |  | STEENBERG | (021) 7011320 |  | (021) 7013179 | 4950116451 |  | 050482
200162 | DK Windowcovers CC |  | SANLAMHOF | (021) 982 6932 |  | (021) 982 6934 | 4920105469 |  | 049271
200164 | Don Gresswell Library Products CC |  | GREYVILLE | 031 3124025 |  | 031 3032248 | 4630102582 |  | 027456 |  | dongresswell@icon.co.za
200168 | The Cape Town Rubber Co Pty Ltd |  | MILNERTON | SALLYCTRUBBER... |  | 021 5110916 | 4800107668 |  | 003778 |  | dorothy@ctrubber.co.za
200172 | Festo Pty Ltd |  | ISANDO | 011 9746741 |  | 011 3924877 | 4350101004 |  | 007412 |  | Tercia_Julyan@FESTO.com
200175 | Cape Twines & Packaging Pty Ltd |  | SALT RIVER | 021 4474352 |  | 021 4479880 | 4940107693 |  | 003794
200176 | Drager South Africa Pty Ltd |  | RIVONIA | 011 0594247 |  | 011 4656953 | 4710111677 |  | 048666 |  | nadja.ferber@draeger.com | 011 0594247
200177 | Cape Union Mart International Pty | Ltd | CAPE TOWN | 021 4645800 |  | 021 4617767 | 4180110761 |  | 003808
200179 | FS Systems Pty Ltd |  | OBSERVATORY | 021 2012240 |  | 021 6851177 | 4350101061 | M Walbrugh | 011673 | 021 6851111 | michaela@fs-systems.co.za | 021 2012240
200181 | Cape Watchmakers Supplies & Tool | PTY LTD | CAPE TOWN | 021 4234217 |  | 021 4261925 | 4400101566 |  | 003824 |  | colin@capewatch.co.za
200183 | Eagle Technology |  | CAPE TOWN | 021 4234943 |  | 021 4244637 | 4450132586 |  | 048208
200185 | Eagle Lighting Pty Ltd |  | CAPE TOWN | 021 5112640 |  | 021 5112645 | 4800195960 |  | 006424
200189 | Capewell Springs Pty Ltd | T/A Capewell Springs | EPPING | 021 5059413 |  | 021 5351047 | 4160103729 | Mrs Sherna Davi | 031232 | 021 5351047 | shernadavids@capewell.co.za | 021 5059406
200190 | The Flower Box |  | TOKAI | 021 7151665 |  | 021 7152088 | 4450145687 |  | 007595 |  | wallander@mweb.co.za
200193 | The Flower Shop |  | KENILWORTH | 021 7623852 |  | 021 7614706 | 4430121402 |  | 007617 |  | flowershop@telkomsa.net
200197 | Kimberly Clark of S A Pty Ltd |  | EPPINDUST | (021) 5302100... |  | (011)4565703 | 4220105342 |  | 051675
200198 | EBV-Electrolink Pty Ltd |  | CAPE TOWN | 021 4021948 |  | 021 4196256 | 4180101760 |  | 006742
200201 | Carl Zeiss Pty Ltd |  | RANDBURG | 011 8869510 |  | 011 8869592 | 4200103044 |  | 014648 |  | lucia.marole@zeiss.co.za
200203 | Carpet & Flooring Services CC |  | CALEDON SQUARE | (021) 4653959... |  | (021) 4653924 | 4940103767 |  | 053872
200209 | Fowkes Bros Pty Ltd |  | CAPE TOWN | 021 5087500 |  | 021 5084920 | 4420101034 |  | 007811 |  | jmabaso@fowkes.co.za
200213 | Emplast Engineering Pty Ltd |  | GOODWOOD | (021) 9327825... |  | (021) 9327819 | 4610155311 |  | 047359
200215 | Eloff Transformers CC |  | CHEMPET | 021 5526800 |  | 021 5526810 | 4420110142 | Tracey Eloff | 006890 | 021 5526810 |  | 021 5526800
200221 | Executive Information Services t/a | Caxton Books | KENILWORTH | 021 6836654 |  | 021 6837669 | 4410103750 |  | 004081 |  | debtors@caxtonbooks.co.za
200223 | Environmental Instruments CC |  | BELVILLE | (021) 9144408 |  |  | 4350206902 | JP Ramackers |  |  | jp@envinst.co.za | 082 4492943
200227 | Eriez Magnetics SA Pty Ltd |  | BOKSBURG | 011 4449160 |  | 011 4449166 | 4590106334 | Paul Nel | 051209 | 011 4449166 | pnel@eriez.co.za | 011 4449160
200229 | Gartech Equipment CC |  | EPPINDUST | (021) 5343388 |  | (021) 5346869 | 4170109625 |  | 056405
200238 | General Medical Supplies CC |  | EDENVALE | 021 9515709 | (021) 5924659 | 021 9515768 | 4650105036 |  | 054089 |  | sonjap@gms.co.za
200241 | Macsteel Trading Pty Ltd |  | BELLVILLE | 021 9505500 |  | 021 9505600 | 4940102116 |  | 019968 |  | Donovan.Hartogh@mactrading.co.za
200247 | Maizey Plastics Pty Ltd | T/A Maizey Plastics | PRETORIA WEST | 021 5119783 |  | 021 5101912 | 4750111470 |  | 052833 |  | tammyb@maizey.co.za
200248 | Ricoh SA Pty Ltd |  | Cape Town | 021 4047100 |  | 021 4470218 | 4880120094 | T Khanyile | 008397 |  | Thembelihle.Khanyile@ricoh-europe.com | 087 353 9835
200251 | Glasschem CC |  | DIE BOORD | 021 8879338 |  | 021 8879343 | 4470133002 |  | 049743 |  | Sarel@glasschem.co.za
200252 | Marcold Refrigeration Co Pty Ltd |  | CHEMPET | (021) 5512119 | 021-5512129 | (021) 5512288 | 4390102202 |  | 012289
200253 | Marcus Medical Pty Ltd |  | CAPE TOWN | 021 4621110 |  | 021 4621042 | 4610101059 |  | 012319 |  | DGorman@marcusmed.co.za
200262 | Gluepaste Manufacturing Co Pty Ltd |  | MAITLAND | (021) 5116036 |  | (021) 5114457 | 4520105521 |  | 008567
200268 | Clover Scales Pty Ltd |  | NORTHRIDING | (021) 5933108 |  | (021) 5939302 | 4120146925 |  | 017221 |  | lucele@cloverscales.co.za
200272 | Medical Electronic Distributors | Pty Ltd | BELLVILLE | 021 9303940 |  | 021 9392219 | 4680148758 |  | 056707
200273 | Club Corporate |  | CAPE TOWN | (021) 4874100 |  | (021) 4221892 | 4170119442 |  | 046868 |  | aziza@corporate1.co.za
200275 | Equity Technologies Pty Ltd |  | PAARDEN EILAND | 021 5316112 |  | 021 5316199 | 4070156551 |  | 054704 |  | bookkeeper@equitech.co.za
200276 | Media Spectrum Pty Ltd |  | BELLVILLE | 021 9482604 |  | 021 9499851 | 4600101176 |  | 027006 |  | info@mediaspectrum.co.za
200278 | Graphic Laminates CC |  | MAITLAND | 021 5105461 |  | 021 5105469 | 4440117028 |  | 053503 |  | tracey@graphiclaminates.co.za
200287 | Comet Transport (Pty) Ltd |  | EPPING INDUSTRY | (021) 5320728 |  | (021) 5320730 | 4560149447 |  | 004936
200292 | Gripper & Co Pty Ltd |  | PLUMSTEAD | 021 4477203 |  | 021 4476981 | 4350101525 |  | 008842 |  | karen@gripper.co.za
200299 | Metalgrapho Technology Pty Ltd |  | CAPE TOWN | 021 5105960 |  | 021 5105969 | 4750175814 |  | 012971 |  | cv@metalgrapho.com
200301 | Cape Metal Window Servicing CC |  | WOODSTOCK | 021 4484333 |  | 021 4472611 | 4710101157 | Fatima Kippie | 012998 | 021 4472611 | accounts@metalwindows.co.za | 021 4484333
200303 | Micro Electric |  | PAROW | 021 9393123 |  | 021 9393174 | 4870103738 |  | 013102 |  | microelec@eagleowl.co.za
200304 | Microsep Pty Ltd |  | BRAMLEY | 021 9140393 |  | 021 9140366 | 4330165772 |  | 013188 |  | mandy.meixieira@microsep.co.za
200310 | The Computer Society of SA |  | HALFWAY HOUSE | (011) 3151319 |  | (011) 3152276 | 4760121113 |  | 005037
200312 | Millners Dental Suppliers Pty Ltd | t/a Wright Millners | CAPE TOWN | (021) 530 8800 |  | (021) 531 1700 | 4210113140 |  | 013196
200316 | Mistral Refrigeration CC |  | TYGERVALLEY | 021 9819200 | (021) 9819201 | 021 9814591 | 4450105491 |  | 052345
200325 | Hamrad Electronics Pty Ltd |  | CAPE TOWN | 021 5552338 |  | 021 5552866 | 4660103765 |  | 047341
200327 | M Pagliari Pty Ltd |  | CAPE TOWN | 021 4237335 |  | 021 4240296 | 4070103819 |  | 014907
200345 | Hawkes & Findlay Pty Ltd |  | OBSERVATORY | 021 4472150 |  | 021 4487709 | 4510102264 | Rabie De Vos | 009113 |  | devos@h-f.co.za | 021 4472150
200356 | Mirrors Galore t/a Peacock Glass |  | MOWBRAY | 021 6863809 |  | 021 6863813 | 4020151413 | Corinne Nelson | 014966 | 021 6863813 | peacockglass@mweb.co.za | 021 6863809
200361 | Non-Ferrous Metal Works SA Pty Ltd |  | MAITLAND | 021 5110286 |  | 021 5117538 | 4370108260 |  | 014265 |  | lindav@nfm.co.za
200363 | Northern Office Services CC |  | BRACKENFELL | 021 9813448 |  | 021 9818350 | 4010105536 |  | 048216 |  | leonie@nos.co.za
200367 | High Energy Processing Cape Pty Ltd | t/a Hepro Cape Pty Ltd | CHEMPET | 021 5558880 |  | 021 5511766 | 4860123761 |  | 051829 |  | elma@hepro.co.za
200369 | Hilti South Africa Pty Ltd |  | HALFWAY HOUSE | (011) 6526500 |  | (011) 6526559 | 4730109107 |  | 055599
200370 | Iepsa Pty Ltd |  | MENLOPARK | 012 3622029 |  | 012 3622030 | 4710104946 |  | 009857 |  | mj@iepsa.co.za
200373 | Ikapa Tours & Travel Pty Ltd |  | OBSERVATORY | 021 5108666 |  | 021 5117622 | 4550142147 |  | 054194 |  | sabrina@ikapa.co.za
200374 | N & Z Instrumentation & Control (Ca | Pty Ltd | PAROW | 021 9399134 |  |  | 4620144354 |  | 014206 |  | cape@nz.co.za | 071 1551296
200375 | Illovo Sugar South Africa Pty Ltd |  | MEREBANK | 031 4507700 |  | 031 4629114 | 4790254926 |  | 042366 |  | GailB@value.co.za
200376 | Hewlett-Packard South Africa |  | WENDYWOOD | 021 7851000 | (021) 6586202 | 021 7851500 | 4840110680 |  | 009342 |  | anita.singh@hp.com
200378 | OMEG Scientific CC |  | SOMERSET WEST | (021) 8529132 |  | (021) 8529132 | 4530125592 |  | 041661 |  | omeg@xsinet.co.za
200379 | Omniform Pty Ltd |  | CLAREMONT | (021) 6741030 |  | (021) 6741594 | 4370116446 |  | 055573
200381 | Banks R & L Hiring |  | MAITLAND | 021 5107011 |  | 021 5107061 | 4220144341 |  | 009407 |  | nisham@banksrl.com
200395 | Paul Bothner Pty Ltd |  | CLAREMONT | (021)6744030 |  | (021)6741897 | 4820101873 |  | 002666 |  | lucilleb@bothner.co.za
200397 | P Dobias Precision Engineering CC |  | BLOUBERGSTRAND | 021 6502519 |  | 021 6504554 | 4150127274 |  | 052647
200401 | Concorde Travel |  | CENTURY CITY | (021) 5277500 |  | (021) 5550524 | 4220112504 |  | 046999
200403 | Leksikons Pty Ltd t/a | Horizon Library Services | PLUMSTEAD | 021 7075700 |  | 021 7075795 | 4130146154 |  | 047724
200408 | H Rohloff Pty Ltd |  | GAUTENG | (011) 7042233 |  | (011) 7045859 | 4870110055 |  | 049387 |  | accounts@hrohloff.co.za
200409 | International Power Products CC |  | Bosmansdam Road, Milnerton | (021) 5514141 |  | (021) 5514354 | 4040154249 |  | 048321 |  | shamiela@ipp.org.za
200412 | Peter Jones Electronic Equipment | Pty Ltd | PINEGOWRIE | (011) 6052213 |  | (011) 6052203 | 4920116060 |  | 010588 |  | nicola@actum.co.za
200413 | Peters Papers Pty Ltd |  | EPPINDUST | 021 5347271 |  | 021 5347282 | 4770217349 |  | 015113 |  | stadenan@peterspapers.co.za
200430 | Pienaar Bros Pty Ltd |  | CAPE TOWN | 021 5118131 |  | 021 5112464 | 4880235074 |  | 015253 |  | debtors@pienaarbros.com
200434 | Jedelect Distributors CC |  | PAARDEN EILAND | (021) 5110262 |  | (021) 5114987 | 4210101160 |  | 010448
200435 | RCL Technologies CC |  | SOMERSET WEST | (021) 8525653 |  | (021) 8525459 | 4360103719 |  | 049042 |  | accounts@rcl.za.net
200441 | Incanox Pty Ltd t/a Johannesburg | Valve & Fitting Co | EDENVALE | 021 5512049 | (011) 6097926 | 021 5512069 | 4020258333 |  | 027960 |  | charlotte.jones@johannesburg.swagelok.com
200442 | Register Screen Pty Ltd |  | PAARDEN EILAND | 021 5114315 |  | 021 5116881 | 4500104502 | Naomi Johnson | 048003 | 021 5116881 | naomij@registerscreen.co.za | 021 5114315
200447 | Powerbase CC |  | CAPE TOWN INTERNATIONAL AIRPORT | 021 3862214 |  | 021 3862505 | 4790108056 |  | 049956 |  | taryn@powerbase.co.za
200450 | Renlaw CC |  | STEENBERG | (021) 7017917 |  | (021) 7017917 | 4640149151 |  | 055557
200451 | Powertool Repairs Pty Ltd |  | WOODSTOCK | 021 4482620 |  | 021 4482600 | 4440194647 |  | 022799 |  | joy@ptrct.co.za
200455 | Rennies Travel |  | CLAREMONT | (021) 6709700 |  | (021) 6742335 | 4650120043 |  | 047139
200465 | Rentokil Initial Pty Ltd |  | CLAREINCH | 021 6704700 |  | 021 6716083 | 4930101318 |  | 016624 |  | portia.sebastian@rentokil-initial.com
200466 | Juta & Company Pty Ltd |  | LANSDOWNE | 021 6592300 |  | 021 6592360 | 4520113319 |  | 010642 |  | acarlse@juta.co.za
200477 | Kilpin Steel Pty Ltd |  | OTTERY | 021 7033002 |  | 021 7033478 | 4770272997 | Denise Martin |  | 021 7033478 | accounts@kilpinsteel.co.za | 021 7033002
200482 | Projector & Sound Services Pty | Ltd | PAROW | 021 9462177 |  | 021 9464048 | 4320101787 |  | 015962 |  | kathy@projectorandsound.co.za
200491 | Protea Electronics Pty Ltd |  | BRAMLEY | 011 7863647 |  | 011 8871479 | 4280199185 |  | 050628 |  | piet@protea.co.za
200492 | Kwikot Ltd - Cape Division |  | EPPINDUST | (021) 543691 |  | (021) 541606 | 4700120373 |  | 011088
200494 | Colsan CC | t/a Revprint Claremont | NEWLANDS | 021 6830883 |  | 021 6837464 | 4250117811 | Sam Brooker |  |  | office@revprint.co.za | 021 6830883
200496 | Rustenburg Pharmacy |  | RONDEBOSCH | 021 6863997 |  | 021 6894210 | 4250105568 |  | 017000 |  | rustenburgpharm@kingsley.co.za
200499 | Laboratory Specialist Services cc |  | CLAREINCH | 021 7123514 |  | 021 7123679 | 4580141564 | Sue V/D Walt | 011177 | 021 7123679 | sue@lss.co.za | 021 7123514
200500 | Labretoria CC |  | WATERKLOOF, PRETORIA | 012 462249 | (012) 466943 | 012 464113 | 4440104893 |  | 011185
200508 | Laughton & Co Pty Ltd |  | WOODSTOCK | 021 457220 |  | 021 451118 | 4640102093 |  | 011371 |  | gwen@laughton.co.za
200509 | T Birch & Co Ltd |  | GRAHAMSTOWN | (046) 6227010 |  | (046) 6222643 | 4630103895 |  | 002240
200514 | Legg & Wessel Packaging CC |  | PAARDEN EILAND | 021 5112001 |  | 021 5112254 | 4650104526 |  | 011452 |  | briar@landw.co.za
200520 | Topfasteners cc t/a Topfast |  | PAARDEN EILAND | (021) 5114477 |  | (021) 5114497 | 4730146661 |  | 049239
200523 | Rags 4 Us cc t/a Trade Wipers |  | SANLAMHOF | (021) 9488741 |  | (021) 9463722 | 4600223996 |  | 047368
200533 | Sportsmans Warehouse |  | CAPE TOWN | (021) 4624444 |  | (021) 4656570 | 4630101840 |  | 011835
200539 | Tru-Temp Air Conditioning CC |  | MAITLAND | (021) 5931177 |  | (021) 5930102 | 4520114663 |  | 054879
200545 | Sabinet Online Ltd |  | CENTURION | 012 6439500 |  | 086 5137903 | 4490163401 |  | 023248 |  | accounts@sabinet.co.za
200555 | African Environmental Solutio |  | CLAREMONT | (021) 7978479 |  | (021) 7978482 | 4790145959 |  | 056138
200561 | Lexshell 155 General Trading Pty Lt | t/a The Scientific Group Pty Ltd | VORNA VALLEY | 087 3535800 |  | 086 5572874 | 4950256992 |  | 041084 |  | mpolaid@Ascendismedical.com
200563 | Scheltema & Co Pty Ltd |  | GATESVILLE | 021 6383121 |  | 0216374671 | 4790101549 |  | 018856 |  | mari@scheltema.co.za
200565 | Schindler Lifts SA Pty Ltd |  | PAARDEN EILAND | 021 5524831 |  | 021 5694349 | 4080245485 |  | 041882 | 086 5694498 | estelle.ellis@schindler.com | 021 5524831
200567 | Scientific Glassblowers CC |  | PINELANDS | (021) 5311586 |  | (021) 5313171 | 4610135313 |  | 011118
200569 | Scientific Manufacturing c.c |  | MILNERTON | (021) 5561975 |  | (021) 5560741 | 4260110871 |  | 017515 |  | info@smc.org.za
200574 | BJ Oberholzer CC |  | CAPE TOWN | 021 4617370 |  |  | 4240102246 | B Obeerholzer | 014443 |  | karl@oberholzerbj.co.za | 021 4617370
200578 | Separation Scientific SA Pty Ltd |  | HONEYDEW | 021 6716748 | (011) 7941335 | 086 7704104 | 4860184037 | Karen Taylor | 015210 |  | debtors@sepsci.co.za
200581 | Shaps Cameraland |  | CAPE TOWN | 021 4234150 |  | 021 4221534 | 4320155197 |  | 017744
200582 | Seartec Trading Pty Ltd t/a | Sharp Electronics | CAPE TOWN | 021 4042600 |  | 021 4042670 | 4430232043 |  | 017752 |  | margaretm@seartec.co.za
200583 | Overwear & Duchess Pty Ltd |  | WOODSTOCK | (021) 4475370 |  | (021) 4470585 | 4430102220 |  | 019992
200586 | Starlight Wholesale Electrical | Suppliers Pty Ltd | WOODSTOCK | 021 4484412 |  | 021 4479373 | 4310181005 |  | 020052 |  | admin@starlightwes.co.za
200588 | Unsgaard & Samson Pty Ltd |  | LANSDOWNE | (021) 6901800 |  | (021) 6901833 | 4830146892 |  | 020125
200592 | Val-Hau et cie Pty Ltd |  | CAPE TOWN | (021) 4483995 |  | (021) 474433 | 4410101846 |  | 053767
200594 | Vecboards CC |  | CAPE TOWN INT AIRPORT | 021 3862214 | (021) 9311113/4 | 021 3862505 | 4300102177 | Selwyn | 024120 | 021 3862505 | selwyn@powerbase.co.za | 021 3862214
200602 | Wap South Africa Pty Ltd |  | AIRPORT INDUSTRIA | (021) 3861855 | (021) 3861856/7 | (021) 3862438 | 4150101006 |  | 032433
200605 | Enviroserv Waste Management Pty Ltd |  | TYGERPARK | 0870868402 |  | 0865041373 | 4050166521 |  | 020583 |  | Annelecia.Sullivan@enviroserv.co.za
200606 | Merck Life Science Pty Ltd | t/a Sigma Aldrich | MODDERFONTEIN | 086 0063725 |  |  | 4510154414 |  | 056979 |  | debtors@merckgroup.com
200607 | Iliad Africa Trading Pty Ltd t/a | W & B Hardware | GLOSDERRY | 021 6707270 |  | 021 6707288 | 4010211375 |  | 020613 |  | admin@wbh.co.za
200611 | Easi-Bind Pty Ltd |  | NEW GERMANY | 021 6975363 |  | 021 6975365 | 4380187023 |  | 030147
200612 | Who's Who Of Southern Africa CC |  | CRAIGHALL | (011) 8802406 |  | (011) 8802366 | 4170106290 |  | 020745
200614 | Whid Power Distributors |  | PAROW | (021) 9304026 |  | (021) 929576 | 4370120877 |  | 048836
200616 | Singer Photographic Services Pty | Ltd | WOODSTOCK | (021)4613258 |  | (021)4615539 | 4590101020 |  | 017922 |  | sales@singerphoto.co.za
200619 | Cape Seating Manufacturers CC |  | MAITLAND | 021 5934110 |  | 021 5930904 | 4100182601 | Mona Rabin | 054649 | 021 5930904 | mona@csm.co.za | 021 5934110
200620 | Skefco Cape Town |  | PAARDEN EILAND | (021) 5117031 |  | (021) 5119622 | 4930101334 |  | 017957
200623 | Wika Instruments Pty Ltd |  | BENROSE | 021 5119228 |  | 021 5115866 | 4020103596 |  | 020826 |  | debtors@wika.co.za
200628 | World Travel Agency Pty Ltd |  | CAPE TOWN | 021 4462600 |  | 021 4462601 | 4710158280 |  | 047090 |  | vadams@carlsonwagonlit.co.za
200630 | Sloth Electronics CC |  | MONTE VISTA | 021 5582917 |  | 021 5591512 | 4300141803 |  | 054267 |  | raymondsloth@telkomsa.net
200631 | World Wide Travel (West Coast) | (Pty)(Ltd) | West Beach | (021) 5560901 |  | (021) 5560922 | 4040172159 |  | 047082
200632 | W Voigt Cape Pty Ltd |  | WETTON | 021 7974290 |  | 021 7975969 | 4920105592 | Lydia Simpson | 024090 | 021 7975969 | wvoigt@mweb.co.za | 021 7974290
200639 | YMS Medical Supplies Pty Ltd |  | CHEMPET | 021 5510838 |  | 021 5510295 | 4850289168 |  | 021032 |  | debtors@yms.co.za
200645 | The Printing Press |  | HOWARD PLACE | 021 6856930 |  | 021 6856748 | 4770101865 |  | 056200 |  | accounts@theprintingpress.co.za
200647 | Gijima Ast Holdings Pty Ltd |  | Centurion | 012 6755000 |  | 012 6755907 | 4880187028 |  | 015164 |  | debtors@gijima.com
200658 | Rubber Stamp & Engraving Co Pty | Ltd | JOHANNESBURG | (011) 8387882 |  | (0110 8348509 | 4770125054 |  | 055417
200663 | Spark & Ellis Pty Ltd |  | CAPE TOWN | 021 4645900 |  | 021 4617767 | 4250215748 | Ray Perel | 018635 | 086 6469185 | ray@sparks.co.za | 021 4041240
200667 | Specialised System Electro | Medical Pty Ltd | JOHANNESBURG | (011) 4448184 |  | (011) 4448171 | 4280127277 |  | 014877
200669 | Specific Heat CC |  | OTTERY | 021 7038130 |  | 021 7038475 | 4490123850 | Fay Ebrahim | 052485 |  | specific@telkomsa.net | 021 7038130
200678 | Wind-o-Wash cc |  | CLAREMONT | 021 7978403 |  | 021 7972098 | 4600121026 |  | 053120 |  | operations@windowash.co.za
200693 | Leco Africa Pty Ltd |  | KEMPTON PARK | 011 9741681 | (021) 9132797 | 011 9741848 | 4180105324 |  | 011479 |  | priscilla@lecoafrica.co.za
200699 | Stuttaford Van Lines Pty Ltd |  | EPPINDUST | 021 5148700 |  | 021 5348846 | 4040183651 |  | 054070 |  | zaida@stuttafordvanlines.com
200700 | Starke Ayres Pty Ltd |  | EPPINDUST | (021) 543231 |  | (021) 6853837 | 4570134421 |  | 018880 |  | ethal@starkeayres.co.za
200703 | CJ. De Wet t/a Suburban Asphalt | & Civils | PLUMSTEAD | (021) 7124840 | (021) 728845 | (021) 7124842 | 4540109206 |  | 056626
200711 | Sweet-Orr & Lybro Pty Ltd |  | ELSIES RIVER | (021) 9326921 |  | (021) 9324934 | 4200101790 |  | 019194 |  | debtors1@sweetorr.co.za
200715 | Olympic Cycle |  | CLAREINCH | (021) 6715008 |  | (021) 6713800 | 4380107690 |  | 014583
200717 | ORCA Industries |  | CLAREMONT | 021 619673 |  | 021 619733 | 4670135906 |  | 054216 |  | duncan@orca-industries.co.za
200718 | Whitehead Scientific Pty Ltd |  | BRACKENFELL | 021 9446460 |  | 021 9495478 | 4440171751 |  | 020672 |  | accounts@whitesci.co.za
200725 | Ashley & Radmore Pty Ltd |  | CLAREINCH | (021) 6717142 |  | (021) 6743238 | 4130101258 |  | 055611
200728 | Fixafax CC |  | CLAREMONT | (021) 6832526 |  | (021) 6832528 | 4820132977 |  | 051152
200730 | Framers Workroom |  | CONSTANTIA | 021 4471538 |  | 086 6643270 | 4320183876 |  | 027529
200733 | Mamacos Curtains CC |  | Vredehoek, Cape Town | (021) 755411 |  | (021) 729813 | 4590203008 |  | 056030 |  | sales@mamacos.co.za
200738 | Fairbridge Arderne & Lawton |  | CAPE TOWN | 021 4057306 |  | 021 4195135 | 4540117811 |  | 056375 |  | pneale@fairbridges.co.za
200744 | STA Travel Pty Ltd |  | SAXONWOLD | (021) 6851808 |  | (021) 6854480 | 4640151231 |  | 053848
200748 | J P Malan Engineering CC |  | CHEMPET | 083 2556142 |  | 021 5526417 | 4710160690 | Babette Malan | 054798 | 021 5575001 | francoisjpm@mweb.co.za | 083 7955001
200754 | Lead Laundry & Catering Pty Ltd |  | CHEMPET | 021 5514586 | (031) 7004060 | 021 5514057 | 4360182168 | Angela Jordaan | 054143 | 021 551 4057 | debtors@lead.co.za | 021 5514586
200755 | Gordons Powertool & Hardware |  | CAPE TOWN | 021 4242350 |  | 021 4231324 | 4930128592 |  | 008648 |  | gordonshardware@webafrica.org.za
200756 | Link Travel Pty Ltd |  | CLAREMONT | (021) 674 3160 |  | (021) 674 3164 | 4920110865 |  | 048062
200760 | RMB Plastic Containers t/a Plastics | for Africa | EDGEMEAD | 021 5515790 |  | 021 5515863 | 4560234793 |  | 054380 |  | accounts@plasticsforafrica.com
200762 | N & K Engravers |  | WOODSTOCK | (021) 4470530 |  | (021) 4470530 | 4600123600 |  | 013730
200763 | Amtech Laboratory Services CC |  | PLUMSTEAD | (021) 7974559 |  | (021) 7616731 | 4790154118 |  | 030910
200766 | Audiovision Holdings t/a Audiovisio |  | CENTURY CITY | (021) 5520895 |  | (021) 5520932 | 4660226178 |  | 053678
200772 | MTN Business Solutions Pty Ltd | t/a MTN Business | WENDYWOOD | (021) 6588717 |  | (021) 6588552 | 4700151758 |  | 056154
200780 | Kooltron Pty Ltd |  | PAARDEN EILAND | 021 5110109 |  | 021 5110128 | 4200102228 |  | 054029 |  | roneller@kooltron.co.za
200781 | South African Archaeological=BLOCKE | Society | VLAEBERG | (021) 243330 |  | (021) 246716 | 4080104542 |  | 018155
200789 | Sight & Sound Pty Ltd |  | BERGVLIET | 021 5101425 |  | 021 5101426 | 4630298695 | Kirstie Barrett | 053979 |  | kirstie@sightandsound.co.za | 084 258 6627
200793 | Bearing Man Group Pty Ltd | t/a BMG | JEPPESTOWN | 021 5081600 |  | 021 5105516 | 4090266570 | Fenton Carelse | 021873 |  | capetown@bmgworld.net | 021 5081600
200802 | Metro Cleaning Services cc |  | MOWBRAY | 021 6861395 | (021) 6861396 | 021 6861397 | 4680166792 |  | 056889 |  | Skhan@metroclean.co.za
200805 | Mindex Stelsels cc |  | MENLO PARK | 012 3489209 |  | 086 5241262 | 4710121817 |  | 056812 |  | office@mindex.co.za
200806 | Ultrasigns |  | PAARDEN EILAND | (021) 5103200 |  | (021) 5103250 | 4280/35387 |  | 051909 |  | info@ultrasigns.co.za
200807 | Bio Tecknik CC |  | TYGERVALLEY | (021) 9764456 | 0828914724 | (021) 9760510 | 4930122710 |  | 047465
200808 | Unitemp CC - Use 205224 |  | LANSDOWNE | 021 7628995 |  | 021 7628996 | 4010125773 |  | 050423 |  | debtors@unitemp.com
200811 | North Tech Services CC |  | GOODWOOD | 021 5933560 |  | 021 5932250 | 4260117160 |  | 041351 |  | sales@ntspcb.co.za
200814 | Warman Africa Pty Ltd |  | KEMPTON PARK | (021) 545421 |  | (021) 546806 | 4560101141 |  | 020591
200817 | W Fearnehough Africa CC |  | RYNFIELD | (021) 5516690 |  | (021) 5516691 | 4810110017 |  | 052507
200821 | Cape Laboratory Services |  | VALYLAND | (021) 7855968 |  | (021) 7852194 | 4030199402 |  | 056588
200831 | Synchron Markings Pty Ltd |  | CHEMPET | (021) 5511790 |  | (021) 5525291 | 4030108916 |  | 019259
200832 | Prospur Travel Agency CC |  | CLAREMONT | (021) 6719040 |  | (021) 6716106 | 4110121128 |  | ,, |  | prospur4@galileosa.co.za
200836 | Tafelberg Furniture Stores Ltd |  | BELLVILLE | 021 9463330 |  | 021 9454507 | 4700101837 |  | 055476 |  | debtors3@tafelberg.co.za
200839 | The Taxpayer Pty Ltd |  | CAPE TOWN | (021) 4245733 |  | (021) 4240534 | 4500251436 |  | 019313
200843 | Promolab Pty Ltd | t/a Separations | RANDBURG | 011 9191000 |  | 011 9191110 | 4520105083 |  | 048429 |  | accounts@separations.co.za
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

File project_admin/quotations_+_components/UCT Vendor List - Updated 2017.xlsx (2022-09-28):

No of Vendors
No of Vendors | 7,260
Vendor | Account group | Name | Clerk Name | Clerk Telephone | Clerk Email | Sales Email | Salesperson | Sales Telephone | Telephone | Mobile Number | Fax
204878 | COMP | Afrolabs Experimental Software | John Mupetami | 021 5522159 | john@afrolabs.co.za | accounts@labs.ws | John Mupetami | 076 7827750 | 021 5522159
801166 | TEMP | EMARALD PANTHER GENERAL TRADING |  |  |  | loretta.romano@gmail.com | Loretta Romano | 0784590808
202352 | COMP | 1st Gear Trading 120 CC | Grace Adams | 021 6716980 |  | olympiclocksmiths@telkomsa.net | Edith Brown | 021 6716980 | 021 6716980 |  | 021 6832077
500239 | IT3 | 2 Oceans Elevator Services CC |  |  | buschga@iburst.co.za | buschga@iburst.co.za |  |  | 021 7034551 |  | 086 5306528
500495 | IT3 | 20 Something Consulting |  |  | info@20somethingconsulting.co.za
500645 | IT3 | 2012/032402/07 (South Africa) Pty L |  |  |  | greg@solaceconsulting.co.za | Greg Cronje | 021 7022238 | 021 7022238 |  | 086 5468228
203324 | COMP | 24 7 Airport Transport Solutions CC |  |  | nadeemj@polka.co.za | kim.stemmet@telkomsa.net |  |  | 021 4218740 |  | 086 6847779
500485 | IT3 | 3Q Printers CC |  |  |  | aldrinb3@gmail.com | Aldrin Boraine | 021 9039572 | 021 9039572
203739 | COMP | 3S Media Pty Ltd |  |  | wandisile@3smedia.co.ca | nomsa@3smedia.co.za | Wandisile Zwakala | 011 2332600 | 011 2332600 |  | 012 2347275
801731 | TEMP | 406 Media CC | Anel Grobler | 083 2570191 | anel@406.co.za | anel@406.co.za | Anel Grobler | 0832570191
204650 | COMP | 46 Durban Road CC | Maria Nagel | 021 4811027 | maria@africanspiritcpt.co.za | mandy@nest.co.za | Manby Hayes | 021 6850829 | 021 6850829
203736 | COMP | 5th Circuit Consultants t/a 5th Cir |  |  |  | natalie@5thcircuit.co.za | Natalie Van Eden | 021 5323456 | 021 5323456 |  | 021 5311957
200005 | COMP | A & A Furnishers |  |  | beulah@aafurnishers.co.za |  |  |  | (021) 4246150 |  | (021) 4233475
202253 | COMP | A & A Hydraulic Door Services |  |  |  | aidanagustyn@gmail.com |  |  | 021 6969479 |  | 021 6965694
800390 | TEMP | A & D Kaste BK |  |  |  | tielman@malco.co.za | TF Malherbe | 021 9815290 | 021 9815290 |  | 021 9822250
800408 | TEMP | A & E Lategan Ceilings & Partitions |  |  |  | mervyn@aeceilings.co.za | M Wessels | 082 4572199 | 021 9057704 |  | 086 6064740
203572 | COMP | A A Wyllie Funeral Undertakers CC t |  |  |  | carol@rednett.co.za | Jo-Anne Pietersen | 021-593 8820 | 021 5938820 |  | 021 5930626
800624 | TEMP | A And J Scientific CC |  | 021 5542362 |  | ajscientific@mweb.co.za |  | 021 5542362 | 021 5542362 |  | 086 5465669
500570 | IT3 | A Breen |  |  |  | breenbrowne@gmail.com | Ann-Marie Breen | 021 7942527 | 021 7942527
500601 | IT3 | A Moodliar | A Moodliar | 021 4816000 | amoodliar@kalseredp.com | amoodliar@kalseredp.com | Anushia Moodliar | 021 4816000 | 021 4816000 |  | 021 4816001
500068 | IT3 | A N Smith |  |  | reubensmith@afrihost.co.za |  |  |  | 021-3745287 |  | 021-3745287
801309 | TEMP | A Season of Film (Pty) Ltd | Riaan Hendricks | 076 4830502 | info@filmseason.co.za | info@filmseason.co.za | Riaan Hendricks | 076 4830502 | 076 4830502
801438 | TEMP | A Stone Designs |  |  | alne@astonedesigns.co.za | alne@astonedesigns.co.za |  |  | 073 4626791
800645 | TEMP | A Vardien |  |  |  | aqeedahvardien21@gmail.com | Aqeedah Vardien | 021 6922178 | 021 6922178
800965 | TEMP | A Wyngaard |  |  |  | adelevoice@gmail.com | Adele Wyngaard | 073 4659504 | 073 4659504
204687 | COMP | A.AFRICA PAVING CC | NISA | 021 4395500 | capetown@bosspaving.co.za | capetown@bosspaving.co.za | NISA | 071 2580326 | 021 4395500 |  | 021 4395554
500437 | IT3 | A.H. Services |  |  |  | ahservices1@gmail.com | Ashraf Petersen | 021 8253750 | 021 8253750 |  | 0865907250
500530 | IT3 | A.K. Andersen |  |  |  | alison@financialfocus.co.za | Alison Andersen | 021 4097043 | 021 4097043 |  | 0865161675
204893 | COMP | A.L. Abbott and Associates Pty Ltd | Y A DAVIES | 021 4486340 | yolande@alabbott.co.za | accounts@alabbott.co.za | Sue-Ellen | 021 4486340 | 021 4486340 |  | 021 4486342
800116 | TEMP | A.W.D. Jongens |  |  |  | jongens@yebo.co.za | A.W.D. Jongens | 021 7945643 | 021 7945643 |  | 021 7945643
801223 | TEMP | A.W.R Smith Process Instrumentation | Monica James | 011 782-7279 | monica@instruments.co.za | gordon@instruments.co.za | Gordon Smith | 011 782-7279 | 011 782-7279 |  | 086 648 7664
800952 | TEMP | A2Z Solutions CC |  |  |  | dave@digivision.co.za | David Short | 021 4221105 | 021 4221105 |  | 021 4221107
800315 | TEMP | AA Bulpitt |  |  |  | info@hrworks.co.za | AA Bulpitt |  | 082 6935544
800513 | TEMP | AACUSC |  |  | sebokediees@tut.ac.za | sebokediees@tut.ac.za |  |  | 012 3824158 |  | 086 6141260
203378 | COMP | AB Sciex South Africa Pty Ltd |  |  |  | brenda.dixon@lifetech.com |  |  | 011 4780411 |  | 011 4780349
800744 | TEMP | Abacus Metals CC |  |  |  | abacus@iburst.co.za |  |  | 021 9332422 |  | 021 9332460
203264 | COMP | Abanto Building Solutions CC | Megan Human | 021 5564692 | absbuildingsolutions@gmail.com | abanto@mweb.co.za | Megan Human | 021 5564692 | 021 5564692 |  | 021 5569503
201000 | COMP | Abbott Laboratories SA |  |  | daphney.nevhutalu@abbott.com | shekaila.botha@abbott.com |  |  | 011 8582000 |  | 011 8582187
801956 | TEMP | Abdul Kader Coenraad | Firdous Essop | 076 5227038 | feedanyl@gmail.com | akcoenraad@gmail.com | Abdul Kader Coe | 0825663521 | 021 7625780
501105 | IT3 | ABDURAOOF SAYED |  |  |  | arauf.sayed@gmail.com |  | 0845975721
801944 | TEMP | Abieda Fataar | Abieda Fataar | 084 6972020 | akhan.za@gmail.com | akhan.za@gmail.com | Abieda Fataar | 084 6972020
801002 | TEMP | Abigail S Davids |  |  |  | abigaildee@telkomsa.net | A.S. Davids | 021 3747268 | 021 3747268 |  | 021 3747268
203444 | COMP | Ablaze Promotions CC |  |  | belinda@ablazepromotions.co.za | belinda@ablazepromotions.co.za |  |  | 021 5514030 |  | 021 5511160
204043 | COMP | Abrach Construction CC | Amien Abrahams | 021 4477869 | abrachcc@mweb.co.za | abrachcc@mweb.co.za | Amien Abrahams | 021 4477869 | 021 4477869 |  | 021 4477559
800127 | TEMP | Abrahamse and Meyer Productions CC |  |  |  | fred@amproductions.co.za | Fred Abrahamse | 021 4651380 | 021 4651380 |  | 021 4651380
501058 | IT3 | Abu G Audit Inc. | Abubakr Ganchi | 083 6662233 | abu@abugaudit.co.za | abu@abugaudit.co.za | Abubakr Ganchi | 0836662233
204886 | COMP | Abundant Life Business Concepts cc | Ryno Gerber | 079 5156261 | ryno@canterburg.co.za | rynogerber.pr@hotmail.com | Ryno Gerber | 079 5156261 | 044 0040008
203783 | COMP | AC Bruwer |  |  |  | accounts@5seasons.co.za | Carina Bruwer | 021 4625111 | 021 4625111 |  | 021 4611134
800137 | TEMP | AC Environmental Products Pty Ltd |  |  | alan@biodome.co.za | alan@biodome.co.za | Alan Cooke | 021 7125440 | 021 7125440 |  | 021 7125442
204441 | COMP | AC Screens & Shutters Pty Ltd | F Van Toorn | 021 5905090 | finance@acscreens.co.za | salesadmin@acsreens.co.za | Freek Van Toorn | 021 5905090 | 021 5905090 |  | 021 5905095
203681 | COMP | Academic Apparel Industries CC |  |  |  | tanya@academicapparel.co.za | Tanya Webbstock | 031 3060628 | 031 3060628 |  | 031 3060629
202235 | COMP | Academic Marketing Services | Mari Brightmore | 011 4477441 | cserve@academicmarketing.co.za | cserve@academicmarketing.co.za | Jeanette Harold | 011 4477441 | 011 4477441 |  | 011 4472314
202495 | COMP | Academy of Science of South |  |  | Nkosinathi@assaf.org.za | philistas@assaf.org.za |  |  | 012 3491697 |  | 012 3492795
801601 | TEMP | Accelerate Cape Town | David Irish | 083 6560678 | david@sbaccountants.co.za | Nikky@acceleratecapetown.com | Nikky Dowding | 076 3816352
204937 | COMP | Access Office Solutions (PTY) Ltd | Denise Watson | 021 5909500 | Denisew@accessoffice.co.za | Garym@accessoffice.co.za | Gary Meyer | 083 2853119 | 021 5909500
800179 | TEMP | Acclaim Coaching and Training CC |  |  |  | accounts@acclaim.co.za | Igshaan Soules | 011 4501674 | 011 4501674 |  | 086 7439254
800430 | TEMP | Accompany Advisory CC |  |  | ali.m@accompanyadvisory.com | ali.m@accompanyadvisory.com | Ali Monadjem | 073 9350605 | 073 9350605 |  | 086 6391188
800812 | TEMP | Ace Lock & Key Services | Ogata Jones | 021 4482828 | acelock@iburst.co.za |  | Ogata Jones | 021 4482828 | 021 4482828 |  | 021 4482857
800998 | TEMP | ACG Architects Pty Ltd |  |  |  | hassan@acgarchitects.co.za | Hassan Asmal | 021 4486615 | 021 4486615 |  | 021 4486621
204115 | COMP | ACG Plasterers CC | S Abrahams | 021 7031060 | shamilla@agccc.co.za | shamilla@agccc.co.za | Shamilla Abrahams | 021 7031060 | 021 7031060 |  | 086 5039041
500578 | IT3 | Achmat Dantie | Ayesha Dantie | 074 5787363 | finishingtouchc.t@gmail.com | achmat786@gmail.com | Achmat Dantie | 084 6133492 | 084 6133492
204353 | COMP | ACI Technical Services Pty Ltd | Lerato Tshuma | 011 5248400 | tshuma@iiah.co.za | maria@acitechnical.co.za | Maria MacFarlane | 082 8493277 | 011 5248400 |  | 011 5248499
800494 | TEMP | Acoustic Solutions CC |  |  |  | info@acousticsoltions.co.za | Pascal | 021 5116839 | 021 5116839 |  | 021 5113480
204720 | COMP | ACTEBIS 400 CC | ELVIGEL VAAS | 086 1112015 | info@thewatercorporation.co.za | info@thewatercorporation.co.za | ELVIGEL VAAS | 084 4998496 | 086 1112015 |  | 086 6552398
205009 | COMP | Action Appointments | Tracy Nyman | 021 7614916 | tracy@actionappointments.co.za | tracy@actionappointments.co.za | Tracy Nyman | 083 3101050 | 021 7614916 |  | 021 6834688
800782 | TEMP | Action Instruments SA CC |  |  | support@aisa.co.za | info@aisa.co.za |  |  | 011 4032247 |  | 011 4030287
802130 | TEMP | Active Blue Trading 254 CC | JP Nathrass | 021 4343358 | manager@intotheblue.co.za | manager@intotheblue.co.za | JP Nathrass | 021 4343358 | 021 4343358
800710 | TEMP | Active Cellular CC |  |  |  | esmerelda@activecellular.co.za | E Oosthuizen |  | 001 8931309 |  | 011 8931309
800442 | TEMP | Active Fire Systems |  |  |  | essex@activefire.co.za | E.J. Cable | 0824949637 | 082 4949637
800960 | TEMP | Activeops Africa Pty Ltd |  |  |  | sarisha.ramlugan@activeops.com |  |  | 011 4471073
802149 | TEMP | Actuarial Society of SA | Renche Jansen | 021 5090099 | rjansen@actuarialsociety.org.za | rjansen@actuarialsociety.org.za | Renche Jansen | 021 5090099 | 021 5090099 |  | 021 5090160
501115 | IT3 | ACTUARIAL SOCIETY OF SOUTH AFRICA | Renche Jansen | 021 5090099 | rjansen@actuarialsociety.org.za | rjansen@actuarialsociety.org.za | RENCHE JANSEN | 021 5090099 | 021 5090099 |  | 021 5090160
800622 | TEMP | ACUHO-I-SAC |  |  |  | acuhoi@up.ac.za |  |  | 012 4202119 |  | 086 6550693
802047 | TEMP | ACVV Huis Moorrees Moorreesburg | Ina Lochner | 022 4331477 | huismoorrees@pcnetmail.co.za | huismoorrees@pcnetmail.co.za | Ina Lochner | 0224331477
801173 | TEMP | Adam Zackon |  |  |  | adam@a2zsoundz.co.za |  | 0796166153
202587 | COMP | Adams & Adams |  |  |  | beata-s@adamsadams.co.za |  |  | 012 4326000 |  | 012 4326599
202926 | COMP | Adams Booksellers Pty Ltd |  |  | capecity@adamsbooks.co.za | capecity@adamsbooks.co.za |  |  | 021 4212462 |  | 021 4182060
204925 | COMP | Adelaide Cupido |  |  |  | adelaide.davids@gmail.com |  | 083 4405354
202006 | COMP | Adi Renovations CC |  |  | adireno@gmail.com | adireno@gmail.com |  |  | 021 4471523 |  | 021 4471523
201984 | COMP | ADI Scientific Pty Ltd t/a Advanced |  |  | kelet@advancedlab.co.za | info@advancedlab.co.za |  |  | 011 4621363 |  | 011 4621466
801409 | TEMP | Adlow Engineering Pty Ltd | Marshall Cyster | 021 9055810 | admin@adlow.co.za | neil@adlow.co.za | Neil Pitt | 082 8858150 | 021 9055810 |  | 021 9055959
204231 | COMP | Adnotes Pty Ltd | Nathi Mbele | 021 4097866 | nathi.mbele@adnotes.co.za | nathi.mbele@adnotes.co.za | Nathi Mbele | 021 4097866 | 021 4097866 |  | 086 6006527
801196 | TEMP | Adrian Steed Communications cc | JO WOODHEAD | 011 7268096 | asteed@netactive.co.za | asteed@netactive.co.za | JO WOODHEAD | 082 5662305
202050 | COMP | ADT Security |  |  | fgamieldien.za@adt.co.za | cdubass@tycoint.com |  |  | 086 1212300 |  | 086 1212305
800922 | TEMP | Adv Brendan Atkins |  |  |  | atkins@law.co.za | BG Atkins | 021 4224689 | 021 4224689 |  | 021 4249689
500562 | IT3 | Adv SJ Harvey | S. Harvey | 021 4222473 | suzanna.harvey@capebar.co.za | suzanna.harvey@capebar.co.za | S. Harvey | 021 4222473 | 021 4222473 |  | 021 4241851
202766 | COMP | Advanced African Technology |  |  | tony@aatech.co.za | tony@aatech.co.za |  |  | 021 7855957 |  | 021 7853791
801395 | TEMP | Adventure Strategic Communications | Jayde Barends | 082 3022244 | jaydebarends@gmail.com | jaydebarends@gmail.com |  |  | 082 3022244
500720 | IT3 | Advocay Aid (Pty) Ltd | Patricia Martin | 021 7854506 | info@advocacyaid.com | info@advocacyaid.com | As above
500433 | IT3 | Advocc CC |  |  |  | advocc@gmail.com | Craig Zimri | 021 3715847 | 021 3715847 |  | 086 6197797
802079 | TEMP | AE Solutions (Pty) Ltd | Cheryl Storm | 012 9405921 | cheryls@aelab.co.za | NadineS@aelab.co.za | Nadine Swiegelaar | 0845018615 | 012 9405921 |  | 087 2317500
201020 | COMP | AEC Amersham Soc Ltd | Yathin Sunker | 011 6916519 | yathin@aecam.co.za | Orders@aecam.co.za | Colleen Tully | 021 4471719 | 021 4471719 |  | 021 4478402
203600 | COMP | Aecom Davis Langdon Africa Pty Ltd |  |  | ctn@davislangdon.co.za | ctn@davislangdon.co.za | Deirdre Mellett | 021 4237840 | 021 4237840 |  | 021 4237841
203955 | COMP | Aecom SA Pty Ltd |  |  | gerrit.bastiaanse@aecom.com | gerrit.bastiaanse@aecom.com | Gerrit Bastiaanse | 021 9507500 | 021 9507500 |  | 021 9507502
800790 | TEMP | Aephoria Investments Pty Ltd | S Kettleborough | 021 7618134 | simon@aephoria.co.za | simon@aephoria.co.za | Simon Kettleborough | 021 7618134 | 021 7618134
203745 | COMP | Aerontec CC |  |  |  | nazlee@aerontec.co.za | Nazlee Ockhuis | 021 6712114 | 021 6712114 |  | 021 6746622
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

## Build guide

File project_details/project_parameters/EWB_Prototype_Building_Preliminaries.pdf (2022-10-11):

Engineers Without Borders
iSondlo Garden Project
Electronics Team

### 26 September 2022

Prototype Building Preliminaries Meeting Attendees:

+ Ethan
+ Heather
+ Muhaimin
+ Thobani

Prototype Building Preliminaries Considerations:

Regarding components and equipment
+ Safety equipment: insulated gloves, helmets
+ Collecting breadboards – donations encouraged
+ Please collect rectangular ice-cream tubs for covering components
+ Types of tools required: - pliers
- strippers
- drill
- soldering iron
- screwdrivers
+ We need to keep record of the items purchased

Regarding Embedded System Design:
+ Draw up flowcharts and diagrams for logic
+ Go through data sheets for components
+ Download Arduino IDE
+ Go through code structure and write code + Verify code
+ Upload to Arduino

Regarding Prototype Integration in Garden:
+ Visit site for dimensioning
+ Pole mount for solar system
+ Consider implications of prototype placement for expansion

Subteam leaders:
+ Controls => Heather
+ Power => Thobani
Subteam leader tasks:
+ Coordinate subteam meetings, site visits and tasks + Ensure that each team member is on the same page + Keep record of tools and equipment

This week:
+ Gantt Chart
+ Site visit (Saturday, 01 October 2022) + Meet with subteam leaders

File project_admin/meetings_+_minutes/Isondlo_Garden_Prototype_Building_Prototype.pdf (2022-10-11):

## PROTOTYPE PRELIMINARIES

## EWB Isondlo Garden Project

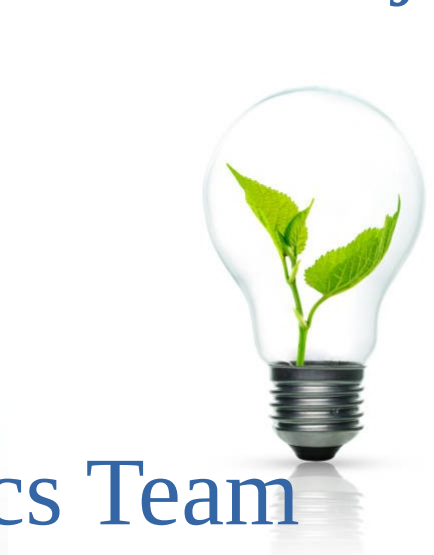
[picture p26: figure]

## Electronics Team

## PROTOTYPE PHASES

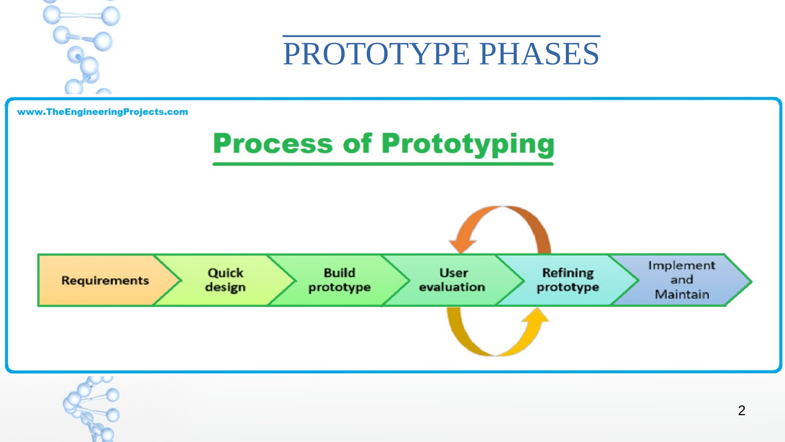
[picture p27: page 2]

## PROTOTYPE PHASES

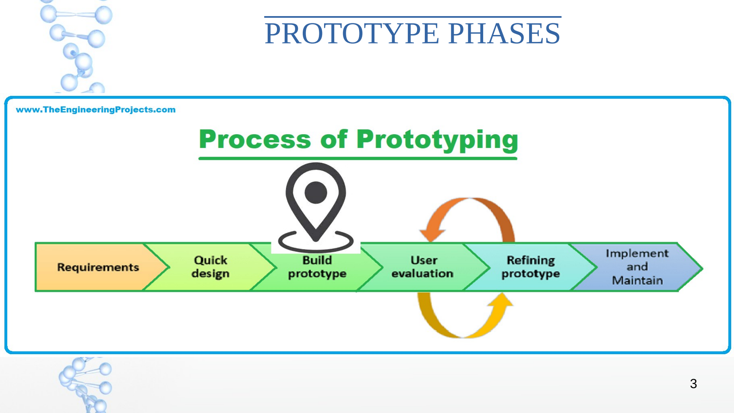
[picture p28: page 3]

## BUILDING THE PROTOTYPE

- Missing components
- Embedded system design
- Component placement considerations
- Cables and wiring specifications

## MISSING COMPONENTS

- SAFETY FIRST!!!
- Breadboards
- Handwork tools such as pliers, strippers, screwdrivers, spanners
- Power tools such as drills, soldering iron

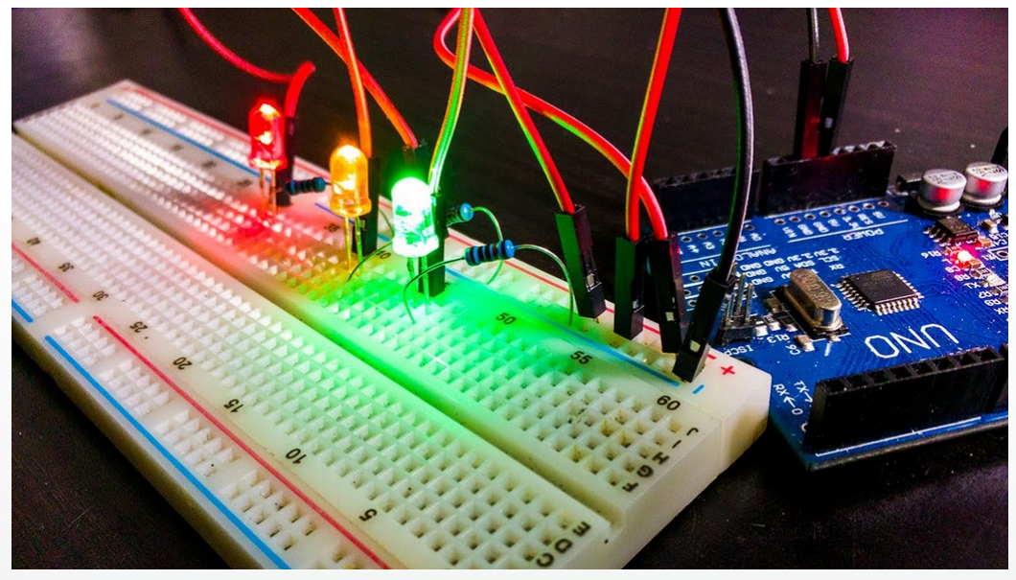
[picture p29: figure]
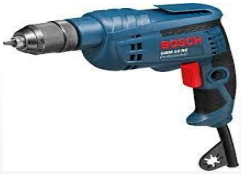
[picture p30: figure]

## EMBEDDED SYSTEM DESIGN

- Flow Diagrams

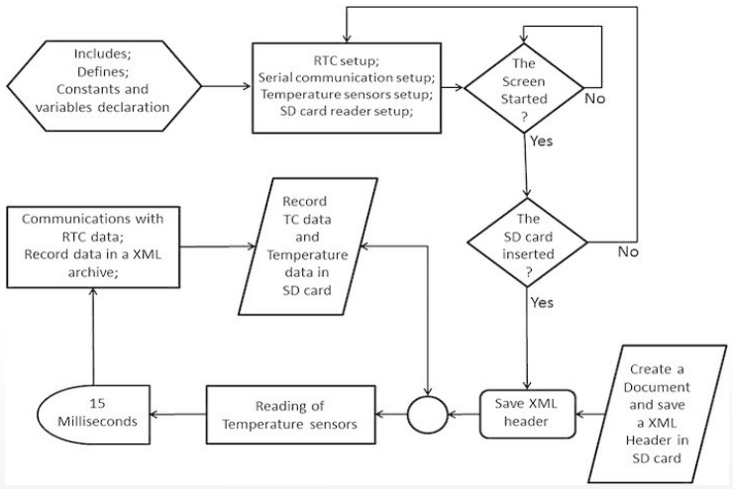
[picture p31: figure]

## EMBEDDED SYSTEM DESIGN

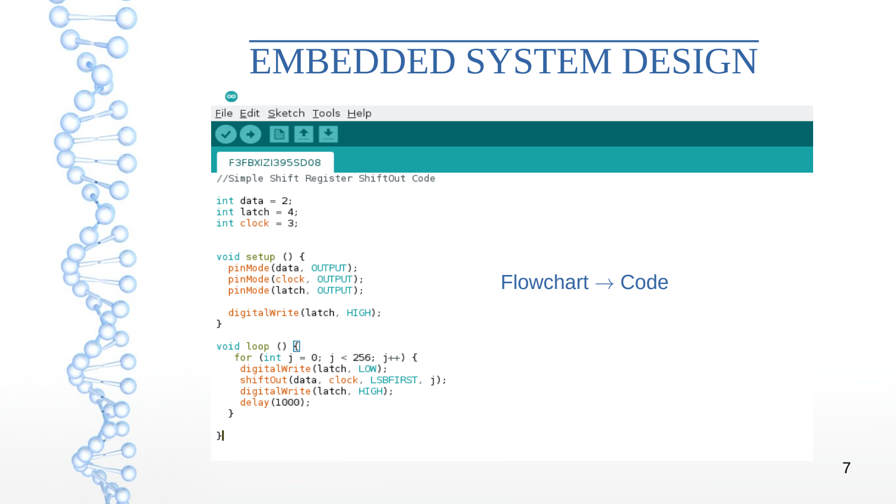
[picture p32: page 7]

Flowchart → Code

## EMBEDDED SYSTEM DESIGN

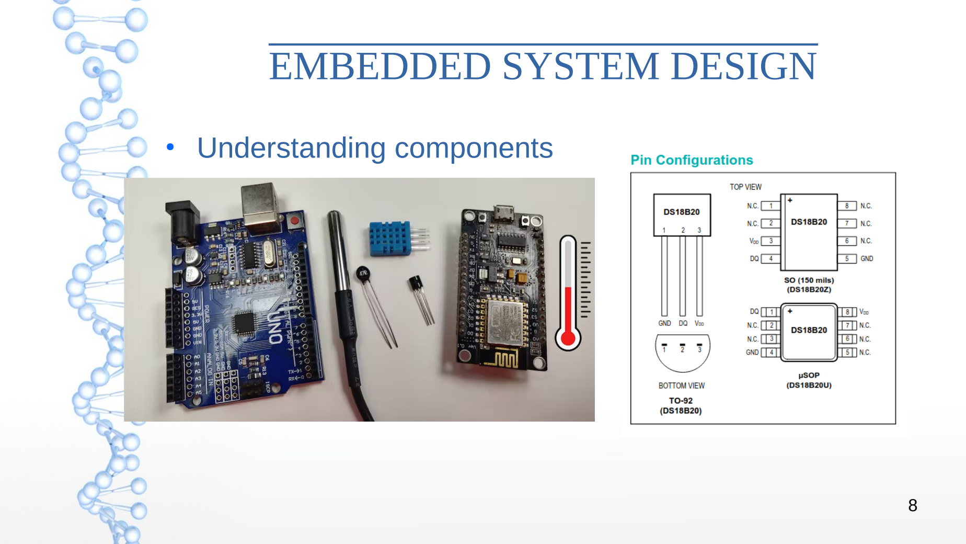
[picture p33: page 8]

- Understanding components

## PROTOTYPE PLACEMENT

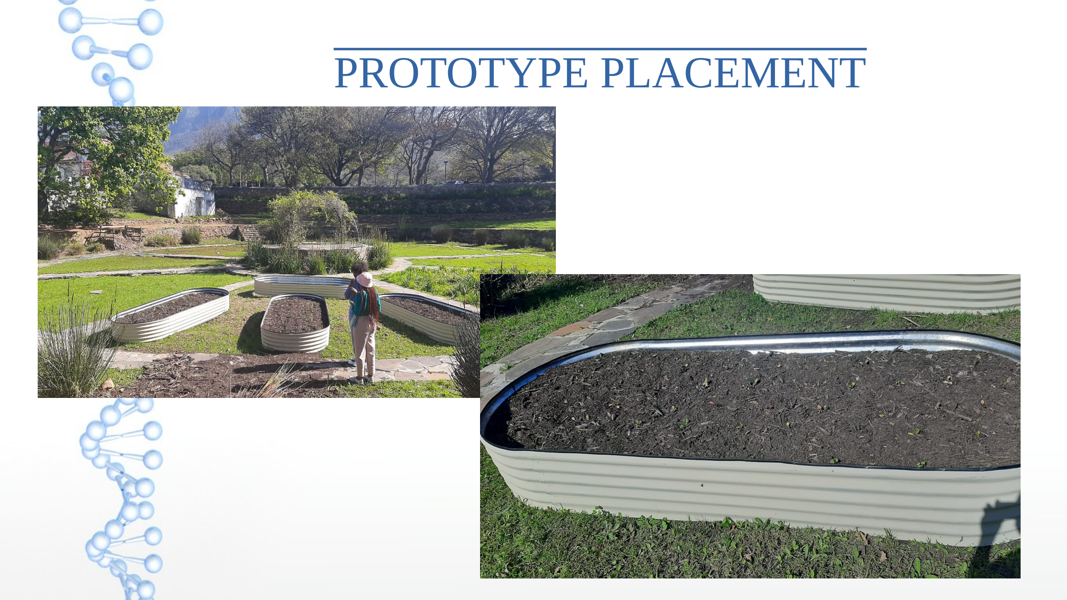
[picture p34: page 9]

## PROTOTYPE PLACEMENT

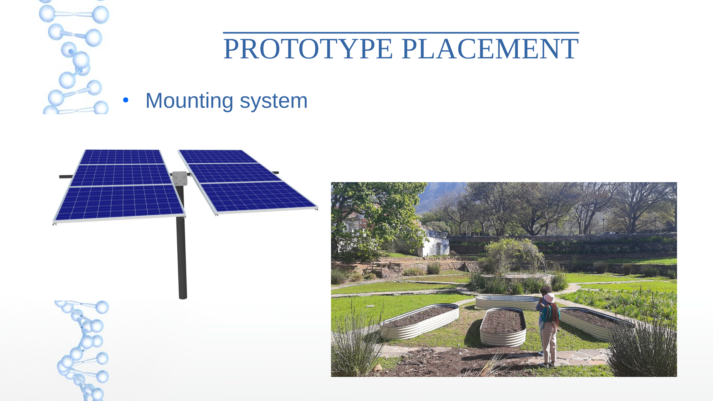
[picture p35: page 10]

- Mounting system

## PROTOTYPE PLACEMENT

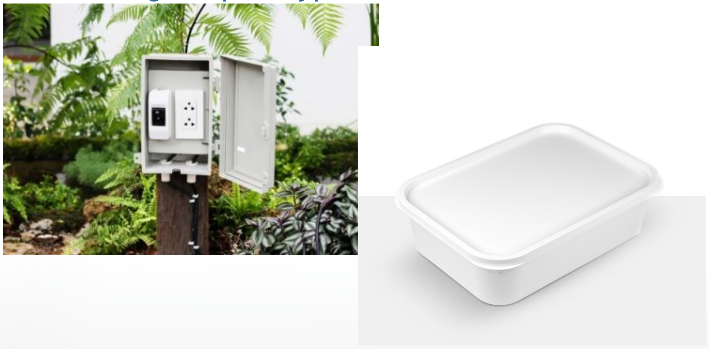
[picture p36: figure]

- Protecting the prototype from the elements

## CABLES AND WIRING

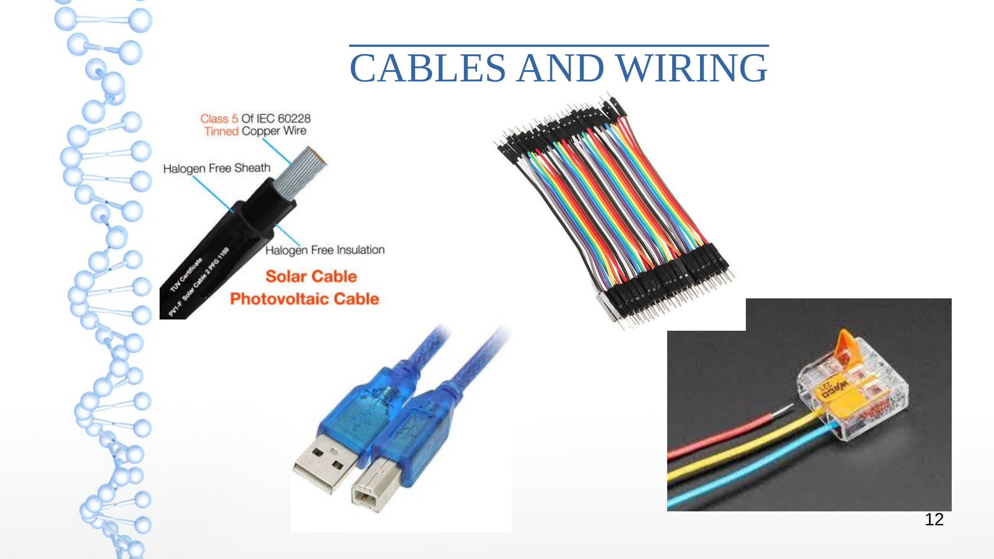
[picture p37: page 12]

## UP NEXT

- Volunteer subgroup leaders
- Draw up Gantt Chart and implement schedule
- Site visit for dimensioning
- Flowchart
- Code

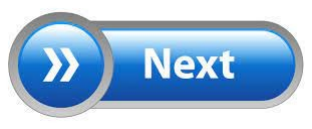
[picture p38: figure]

- Gather all components and required tools
- BUILD!!!

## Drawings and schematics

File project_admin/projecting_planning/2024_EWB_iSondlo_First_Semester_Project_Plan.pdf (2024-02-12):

# 2024 iSondlo Garden Project Timeline

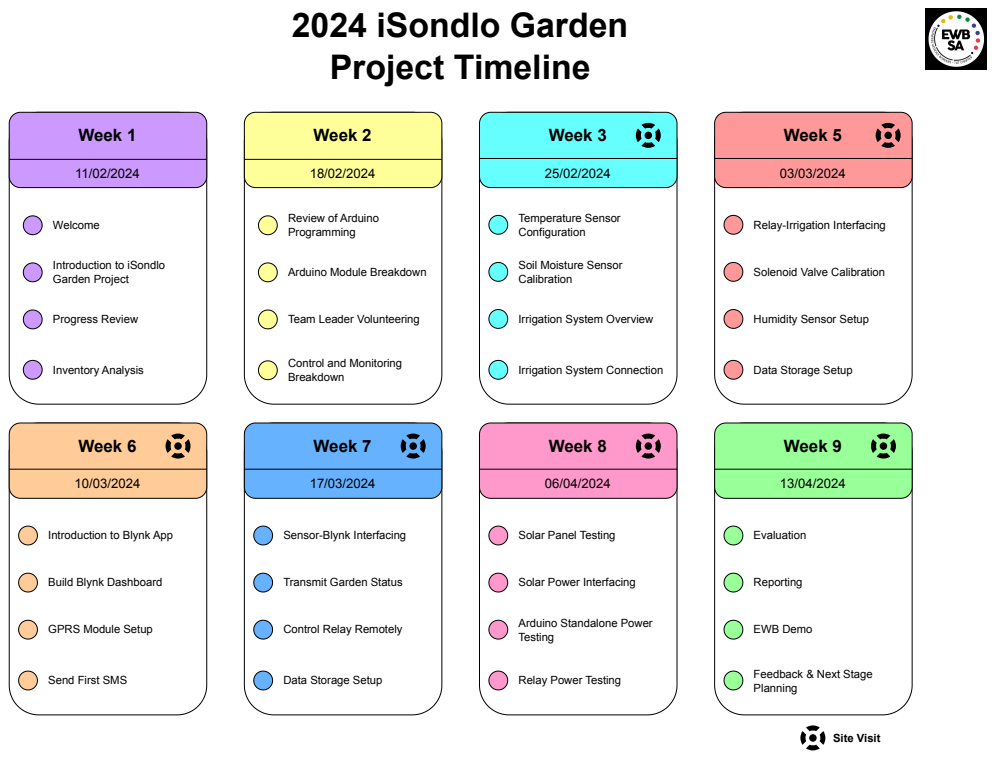
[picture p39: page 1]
Week 1; Week 2; Week 3; Week 5; Welcome; Progress Review; Inventory Analysis; Temperature Sensor Configuration; Week 6; Week 7; Site Visit; Week 8; Week 9; Reporting; EWB Demo; Evaluation

Review of Arduino
Programming

Relay-Irrigation Interfacing

Introduction to iSondlo
Garden Project

Arduino Module Breakdown

Soil Moisture Sensor
Calibration

Solenoid Valve Calibration

Team Leader Volunteering

Irrigation System Overview

Humidity Sensor Setup

Control and Monitoring
Breakdown

Irrigation System Connection

Data Storage Setup

Introduction to Blynk App

Sensor-Blynk Interfacing

Solar Panel Testing

Build Blynk Dashboard

Transmit Garden Status

Solar Power Interfacing

GPRS Module Setup

Control Relay Remotely

Arduino Standalone Power
Testing

Send First SMS

Relay Power Testing

Feedback & Next Stage
Planning

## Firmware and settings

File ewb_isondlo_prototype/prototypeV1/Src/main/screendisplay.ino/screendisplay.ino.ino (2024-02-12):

/*
  LiquidCrystal Library - Hello World

 Demonstrates the use a 16x2 LCD display.  The LiquidCrystal
 library works with all LCD displays that are compatible with the
 Hitachi HD44780 driver. There are many of them out there, and you
 can usually tell them by the 16-pin interface.

 This sketch prints "Hello World!" to the LCD
 and shows the time.

  The circuit:
 * LCD RS pin to digital pin 12
 * LCD Enable pin to digital pin 11
 * LCD D4 pin to digital pin 5
 * LCD D5 pin to digital pin 4
 * LCD D6 pin to digital pin 3
 * LCD D7 pin to digital pin 2
 * LCD R/W pin to ground
 * LCD VSS pin to ground
 * LCD VCC pin to 5V
 * 10K resistor:
 * ends to +5V and ground
 * wiper to LCD VO pin (pin 3)

 Library originally added 18 Apr 2008
 by David A. Mellis
 library modified 5 Jul 2009
 by Limor Fried (http://www.ladyada.net)
 example added 9 Jul 2009
 by Tom Igoe
 modified 22 Nov 2010
 by Tom Igoe
 modified 7 Nov 2016
 by Arturo Guadalupi

 This example code is in the public domain.

*/

// include the library code:
#include <LiquidCrystal.h>

// initialize the library by associating any needed LCD interface pin
// with the arduino pin number it is connected to
const int rs = 12, en = 11, d4 = 5, d5 = 4, d6 = 3, d7 = 2;
LiquidCrystal lcd(rs, en, d4, d5, d6, d7);

void setup() {
  // set up the LCD's number of columns and rows:
  //lcd.begin(16, 2);
  // Print a message to the LCD.
  
}

void loop() {
  // set the cursor to column 0, line 1
  // (note: line 1 is the second row, since counting begins with 0):
  lcd.print("Sunshine!");
  lcd.setCursor(0, 1);
  // print the number of seconds since reset:
  lcd.print(millis() / 1000);
}

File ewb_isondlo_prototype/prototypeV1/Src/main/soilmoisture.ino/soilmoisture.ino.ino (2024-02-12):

#include <LiquidCrystal.h>

//Constant values
const int rs = 12, en = 11, d4 = 5, d5 = 4, d6 = 3, d7 = 2;
const int sensorPin = A0;
const int dry = 632;
const int wet = 309;

LiquidCrystal lcd(rs, en, d4, d5, d6, d7);

int sensorValue = 0;         // the sensor value
int sensorMin = 309;        // minimum sensor value
int sensorMax = 632;           // maximum sensor value


void setup() {
  lcd.begin(16, 2);
  lcd.print("Soil Moisture (%)");
  Serial.begin(9600);
}

void loop() {  
  sensorValue = analogRead(sensorPin);
 
  sensorValue = constrain(sensorValue, sensorMin, sensorMax);

  int percentageHumidity = map(sensorValue, wet, dry, 100, 0);
  
  lcd.setCursor(0, 1);
  lcd.print(percentageHumidity);
  delay(100);
}

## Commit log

2022-09-28 Add files via upload
    Added components lists v1 and v2, prototype v1 and the UCT vendor's list.
    [UCT Vendor List - Updated 2017.xlsx]
2022-10-02 Add files via upload
    First sight measurements. Requires update if the container closest to the center can be used for the prototype.
2022-10-02 Add files via upload
    Added data sheet for Arduino UNO R3 for coding
2022-10-03 Add files via upload
    Added template header files to configure all the sensors and modules to connect to the arduino. Also included datasheets for each module and the arduino.
2022-10-08 Update RemoteConnectionConfig.h
    Declared the configuration functions to setup, start and reset the network connection of the Arduino.
2022-10-08 Update TemperatureSensorConfig.h
    DS18B20 setup header file. Added setup(), lower_trigger and upper_trigger functions.
2022-10-11 Add files via upload
    Organised file related to project administration into one folder
    [UCT Vendor List - Updated 2017.xlsx]
2022-10-20 I moved the Arduino datasheet into the datasheets folder under the ewb_isondlo_prototype
2023-07-19 Add files via upload
    Schematic showing how the arduino uno r3 is connected to the sensor, storage and gprs shield modules in the iSondlo prototype v1.0.0. Sensors include temperature, humidity, light and soil moisture se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
    [controls_schematic.kicad_sch]
2023-08-03 Updated code
    [All Vendors_UCT_2023.XLSX, controls_schematic.kicad_sch]
2024-01-30 Added sensor modules.
    Included temperature sensor module, screen display module as well as temperature sensor module.
